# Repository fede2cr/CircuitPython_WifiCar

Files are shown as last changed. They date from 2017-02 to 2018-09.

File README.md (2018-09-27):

# Guía de construcción y uso del WifiCar con CircuitPython

# For english go to [this version](https://github.com/fede2cr/CircuitPython_WifiCar/blob/master/README.en.md)

## Instrucciones
### Realizar conexión física

Se recomienda que el soldado de los stacking headers y terminales sea realizado previo al taller. De esta forma la única herramienta necesaria sería un desatornillador de punta phillips para ensamblaje del chasis.

- Soldar stacking headers en el ESP8266 y el Featherwing para motor
- Soldar terminales de tornillo en Featherwing para motor
- Poner baterías en holder
- Conectar holder de baterías a puerto de batería para motor, del Featherwing para motores

La tarjeta debería verse de esta forma:

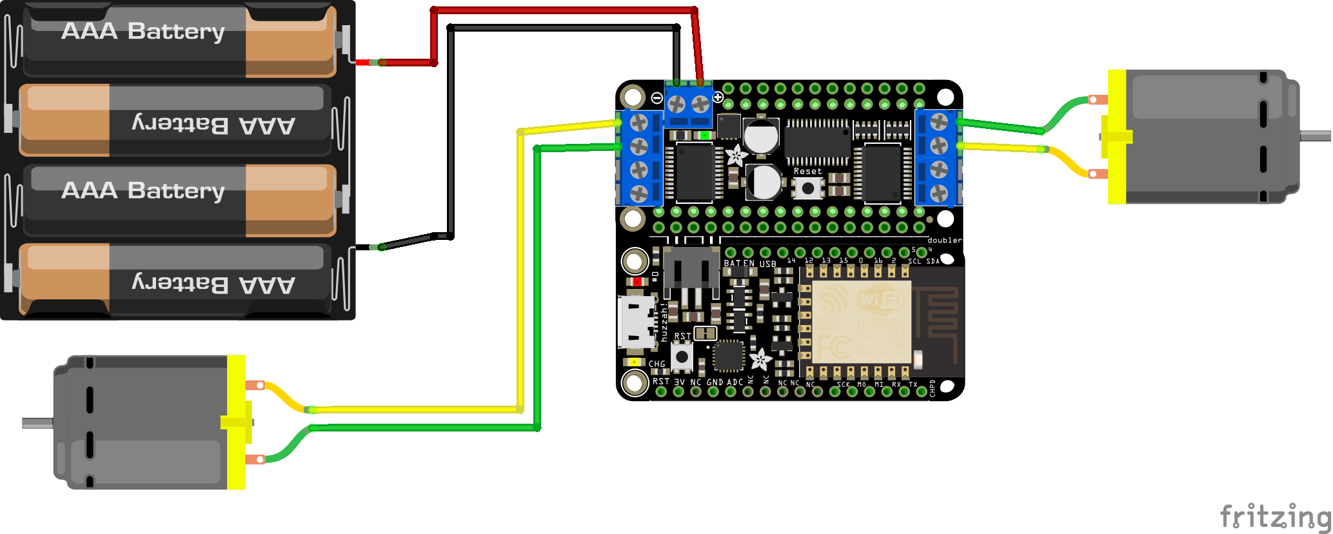
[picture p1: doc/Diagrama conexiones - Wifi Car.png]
Diagrama de Fritzing


### Instalar CircuitPython en ESP8266

Se carga firmware según [instrucciones de Adafruit](https://learn.adafruit.com/micropython-basics-how-to-load-micropython-on-a-board/?view=all#esp8266), pero usando release de CircuitPython

```bash
esptool.py --port /dev/ttyUSB0 erase_flash
esptool.py --port /dev/ttyUSB0 --baud 460800 write_flash --flash_size=detect 0 adafruit-circuitpython-feather_huzzah-es-4.0.0-alpha.1.bin
```
Reiniciar el ESP8266, y comprobar que se puede acceder al REPL de CircuitPython, conectándose al puerto serial
```
screen /dev/ttyUSB0 115200
```
Puede salir de screen digitando ``CTRL+A`` y luego ``:quit``.

### Módulos de CircuitPython

Luego debe descargar los módulos de CircuitPython de Featherwing de motor, de Register Bus Device; los cuales tanto para evitar una [pulga](https://github.com/adafruit/Adafruit_CircuitPython_PCA9685/issues/3) como para simplificar, vamos a utilizar el ["Bundle"](https://github.com/adafruit/Adafruit_CircuitPython_Bundle/releases). Luego utilice la herramienta de ``ampy`` para subir las **carpetas** de los módulos al flash de la ESP8266:

```bash
export AMPY_PORT=/dev/ttyUSB0
unzip adafruit-circuitpython-bundle-2.*.zip
ampy put lib 
ampy ls
```
Ahora puedes probar un pequeño "hola mundo" para comprobar que has subido los módulos de forma correcta, y que has conectado correctamente las baterías y motores. Para esto debes ejecutar de nuevo el comando de `screen` para entrar en el REPL de CircuitPython.
**Nota: Si todo funciona correctamente, el carro se va a mover hacia adelante. Acomódelo de forma que no se caiga de la mesa de trabajo**
```python
from board import *
import bitbangio as io
i2c = io.I2C(SCL, SDA)
from adafruit_pca9685 import motor
motors = motor.DCMotors(i2c)
motors.speed(0, 2000)
motors.speed(3, 2000)
```
*Nota: Es posible que el número del motor haya cambiado, por lo que puedes probar cambiando el motor a mover*
Habiendo comenzado a moverse, el robot solo se va a detener hasta que se agoten las baterías. Para ello digitamos el siguiente comando por cada motor, para iniciar el frenado:

```python
motors.brake(0)
motors.brake(3)
```

### Acceso por Wifi
Esta es una parte que también puede ser preconfigurada en la tarjeta antes de entregar al estudiante, dependiendo de la naturaleza del laboratorio a realizar.
A como viene el firmware de CircuitPython de Adafruit, el ESP8266 se va a comportar como un Access Point wireless, por lo que queremos conectarlo a la red a utilizar durante el curso o taller. También es importante que se configure antes de pasar al sección de WebREPL.

Es importante que la configuración de Wifi no debe ser guardada en `boot.py` dado que es almacenada de forma interna por CircuitPython. Para ello ejecutamos desde el REPL.

```python
import network
wlan = network.WLAN(network.STA_IF)
wlan.active(True)
wlan.connect('nombre-AP-curso','clave-segura')
```
Luego de unos segundos estará conectado a la red, lo que puede comprobar ejecutando:
```python
wlan.ifconfig()
```

### WebREPL
El WebREPL ya casi se encuentra listo para ser usado. Primero debes importar el módulo de `webrepl_setup` el cual se encarga de habilitar WebREPL de forma permanente, así como definir una contraseña de acceso.

*Nota: CircuitPython no tiene límite de conexiones por lo que es fácilmente atacable por fuerza bruta con listas de diccionario. Por ello, fuera de un ambiente académico se recomienda o utilizar una contraseña segura o deshabilitar WebREPL*.

```python
>>> import webrepl_setup
WebREPL daemon auto-start status: disabled

Would you like to (E)nable or (D)isable it running on boot?
(Empty line to quit)
> e
To enable WebREPL, you must set password for it
New password: greencore
Confirm password: greencore
Changes will be activated after reboot
Would you like to reboot now? (y/n) y

```

Luego de este paso, la tarjeta debería reiniciar automáticamente y dejarnos con el WebREPL activado. Por [mientras](https://github.com/adafruit/circuitpython/issues/98) debes reiniciar la tarjeta manualmente presionando el botón de RESET ya sea en la ESP8266 o en el Featherwing de motores.

Para accesar el WebREPL normalmente deberíamos bajar un  [cliente desde esta dirección](https://github.com/micropython/webrepl/archive/master.zip), descomprimir, y abrir con Firefox o Chromium. Defines el IP que tiene actualmente el ESP8266, presionas *Conectar* y digitas la contraseña definida. Ya puedes digitar comandos en la microcontroladora desde el WebREPL, incluidos comandos para los motores y otros. En este proyecto sin embargo se ha incluído funcionalidad Web para que la página de WebREPL sea servida directamente desde la ESP8266.

Así mismo vamos a agregar código a `boot.py` para que pueda servir su propio repositorio de WebREPL para no necesitar un servidor adicional o conexión a Internet. El código de ello se basa en [replserver](https://github.com/ShrimpingIt/cockle/blob/master/replserver/)

Para subir el WebREPL auto-servido, debemos agregar la página web minimizada y comprimida, ejecutando:
```bash
ampy put webrepl-inlined.html.gz
```

### Autoconfiguración

Para evitar que tengamos que digitar las operaciones que definen el motor, vamos a agregar estos comandos iniciales al archivo `boot.py` de forma que cuando inicie la micro, automáticamente va a configurar la tarjeta de motor shield, para que sea más sencillo y podamos digitar comandos de motores de forma directa.

Para ello es buena idea revisar si nuestro archivo `boot.py` posee algún código importante, sin embargo en nuestro caso como hemos comenzado desde cero, es posible omitir este paso. Para revisarlo puede ejecutar:
```bash
ampy get boot.py
```
En nuestro caso, vamos a usar el archivo como base, descomentando las líneas que deshabilitan *debugging*, el cual se encuentra habilitado porque CircuitPython se encuentra en un estado muy activo de desarrollo.
Agregamos las líneas de iniciado de motor y librerías que vimos arriba, y subimos el archivo a nuestra ESP8266.
```bash
ampy put boot.py
```

Después de reiniciar nuestro ESP8266 ya podemos ejecutar comandos de motores:
```python
motors.speed(0, 2000)
motors.speed(3, 2000)
```
Recuerde que el comando actual no ejecuta ningún frenado por lo que luego debe ejecutar:

```python
motors.brake(0)
motors.brake(3)
```

### Clase de Python para manejo de carro

Hasta el momento tenemos un carro que podemos controlar vía Web sobre Wifi. Sin embargo los controles de dicho carro son un poco diferentes a las formas como conducimos algún tipo de carro eléctrico, ya sea de control remoto, un GoCart o un Tesla.

Para ello se crea una pequeña clase de Python donde se pueda controlar de forma sencilla. Se asume que el robot no tiene sensores como giroscopios o rotary encoder, por lo cual algunos movimientos deben ser calibrados y aproximados.

El cargado de esta clas ya se ejecuta automáticamente al inicio del robot por medio de `boot.py`.

Para cargar la clase debe ejecutar en la terminal:
```bash
ampy put Robot.py
ampy ls
```
Ahora puede conectarse al robot usando ya sea `screen` o WebREPL, y dentro ejecutar:

```python
carro.adelante(segundos)
carro.izquierda(segundos)
carro.hola() # Un demo mínimalista
```

También se pueden crear geometrías sencillas definiendo la **cantidad de lados**, el **largo de las líneas en segundos**, y el **tiempo que debería durar girando para hacer el ángulo correcto**. Es importante calibrar el tiempo para el ángulo dado que va a cambiar según la superficie, tracción de las ruedas y carga/tipo de baterías para los motores:
```python
carro.geometria(3, 1, 0.9) # Un triángulo pequeño
carro.geometria(4, 2, 0.7) # Un cuadrado
```

Así mismo, se deben crear demostraciones de comportamiento, las cuales pueden ser cargadas como una clase de ejemplos:
```python
carro.demo(sillywalks) # Como MonthyPython
carro.demo(wifitaxa)   # Camina hacia el access point
```

## Referencias
- [Corriendo código y uso de Ampy](https://learn.adafruit.com/micropython-basics-load-files-and-run-code/?view=all)
- [Featherwing de motores](https://learn.adafruit.com/micropython-hardware-pca9685-dc-motor-and-stepper-driver/?view=all)
- [WebREPL](https://learn.adafruit.com/micropython-basics-esp8266-webrepl/?view=all)
- [TonyD's WebREPL Robot](https://www.youtube.com/watch?v=hOwReBsHq7g)
- [replserver](https://github.com/ShrimpingIt/cockle/blob/master/replserver/)

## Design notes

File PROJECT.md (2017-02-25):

# CircuitPython_WifiCar
Carro controlado por medio de Wifi, basado en la micro ESP8266 con el lenguaje educativo CircuitPython, basado en Micropython

Este documento describe las labores a realizar. Una vez que el proyecto tenga avance, el documento [HOWTO.md](https://github.com/fede2cr/CircuitPython_WifiCar/blob/master/HOWTO.md) reemplazará buena parte de este README.

## Descripción
Greencore Solutions ya tiene un curso de robótica para niños basado en micros Arduino, donde los estudiantes construyen su carro de dos motores el cual es manejado con un control remoto infrarojo, al cual queremos mejorar lo siguiente:

1. El control infrarojo de un estudiante acciona los carros de otros estudiantes por lo que necesitamos cambiar la forma de control remoto.
2. El lenguaje de Arduino se basa en C/C++ por lo que no es la mejor opción para estudiantes completamente novatos. Para ello se recomienda migra a MicroPython o mejor aún a CircuitPython.
3. La micro ofrecida anteriormente tenía un acelerómetro lo que permitía que estudiantes avanzados comenzaran a hacer detección de golpe y otros comportamientos. La micro actual es un poco básica por lo que requiere hardware adicional para permitir que sea interesante para estudiantes avanzados.

## Propuesta
Cambiar a la plataforma de [Feather de Adafruit](https://www.adafruit.com/feather), con los siguientes componentes:

- Adafruit ESP8266 Feather: La plataforma ESP8266 es compatible con Arduino si fuera necesario, tiene conector JST para batería (con capacidad de cargar baterías Lipo), capacidades de red inalámbrica Wifi, así como trabaja con CircuitPython/Micropython.
- Adafruit DC Motor+Stepper Featherwing: Tiene capacidad de hasta cuatro motores lo que permite usar cualquier de los chasis disponibles en [CrCibernetica](http://crcibernetica.com/).

### Cambios menores:
- Cambiar lugar de baterías AAA por posición más accesible. Actualmente hay que desarmar parcialmente el robot para cambio de baterías. Es posible alimentar los motores de 4.5VDC a 13.5VDC por lo que se podría cambiar a baterías 9V u otras.

## Plan de trabajo
- [x] Alistar componentes de hardware: Soldar stacing headers en Feather y Featherwing, remover placa anterior, alistar conectores de batería.
- [x] Instalar última versión de CircuitPython en la ESP8266
- [x] Ensamblar robot con nueva micro y realizar control básico de motores.
- [x] Usar como base WebREPL para crear una librería que permita control del robot por medio de una página web servida por el mismo ESP8266.
- [ ] Crear documentación visual de ensamblaje de robot.
- [ ] Crear diversos laboratorios que el estudiante pueda seguir para sacarle un mejor provecho a su robot ensamblado y completo.
- [ ] Crear traducciones de la documentación
- [ ] Crear clases que permitan crear alias para comandos en otros idiomas (forward=adelante, etc)
- [ ] Probar librería de selector de Wifi, para mejorar la portabilidad del proyecto

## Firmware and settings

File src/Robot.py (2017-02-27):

# RobotControl
# Cualquier posible sensor va a estar apagado por omisión
# Los comandos de movimiento deberían ser similares a los de LogoWriter

# Uso ejemplo:
#   import Robot
#   robot = Robot.Control(motors)
#   robot.adelante(10)
# Autor: Alvaro Figueroa (alvaro@greencore.co.cr)
import time

class Control:
    def __init__(self, motors):
        self._motors = motors
        self._motors.brake(0)
        self._motors.brake(3)

    def adelante(self, secs):
        self._motors.speed(0,2000)
        self._motors.speed(3,2000)
        time.sleep(secs)
        self._motors.brake(0)
        self._motors.brake(3)

    def atras(self, secs):
        self._motors.speed(0,-2000)
        self._motors.speed(3,-2000)
        time.sleep(secs)
        self._motors.brake(0)
        self._motors.brake(3)

    def derecha(self, secs):
        self._motors.speed(0,2000)
        self._motors.speed(3,-2000)
        time.sleep(secs)
        self._motors.brake(0)
        self._motors.brake(3)

    def izquierda(self, secs):
        self._motors.speed(0,-2000)
        self._motors.speed(3,2000)
        time.sleep(secs)
        self._motors.brake(0)
        self._motors.brake(3)

    def hola(self):
        self.adelante(1)
        self.atras(1)
        self.derecha(1)
        self.izquierda(1)

    def geometria(self, lados, largo_secs, angulo_secs):
        for i in range(lados):
            self.adelante(largo_secs)
            self.izquierda(angulo_secs)

    def sillywalk_serpiente(self,secs):
        for i in range(4):
            self._motors.speed(0,4000)
            self._motors.speed(3,2000)
            time.sleep(secs/8)
            self._motors.speed(0,2000)
            self._motors.speed(3,4000)
            time.sleep(secs/8)
        self._motors.brake(0)
        self._motors.brake(3)

    def sillywalk_turn(self,secs):
        for i in range(4):
            self._motors.speed(0,4000)
            self._motors.speed(3,-4000)
            time.sleep(secs/8)
            self._motors.speed(0,-4000)
            self._motors.speed(3,4000)
            time.sleep(secs/8)
        self._motors.brake(0)
        self._motors.brake(3)


    def ayuda(self):
        print("""Modulo de control de robot.
Comandos:
carro.hola()                    Realiza una demostracion de movimientos
carro.adelante(segundos)        Avanza la cantidad de segundos que se indique
carro.atras(segundos)           Retocede la cantidad de segundos que se indique
carro.derecha(segundos)         Gira sobre su eje a la derecha, la cantidad de
                                segundos que se indique
carro.izquierda(segundos)       Gira sobre su eje a la izquierda, la cantidad de
                                segundos que se indique
carro.geometria(lados,
   largo_secs, angulo_secs)     Le indicamos la cantidad de lados, que tan
                                largos en segundos, cuanto tiempo durar girando,
                                y nos crea una figura geometrica

Ejemplos:
carro.hola()
carro.adelante(2)
carro.izquierda(1)
carro.atras(3)
carro.geometria(4, 2, 0.7)
Puede encontrar informacion adicional en
https://github.com/fede2cr/CircuitPython_WifiCar/""")

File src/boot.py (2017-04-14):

# This file is executed on every boot (including wake-boot from deepsleep)
import esp
esp.osdebug(None)
import gc
gc.collect()

import network
wlan = network.WLAN(network.STA_IF)
wlan.active(True)

from board import *
import bitbangio as io
i2c = io.I2C(SCL, SDA)
from adafruit_pca9685 import motor
motors = motor.DCMotors(i2c)
motors.brake(0)
motors.brake(3)

import Robot
carro = Robot.Control(motors)

# replserver boot code
try:
    import usocket as socket
except:
    import socket

import os
import webrepl
webrepl.start(password='greencore')
replpath = "webrepl-inlined.html.gz"

s = socket.socket()
ai = socket.getaddrinfo("0.0.0.0", 80)
addr = ai[0][-1]

s.setsockopt(socket.SOL_SOCKET, socket.SO_REUSEADDR, 1)
s.bind(addr)
s.listen(5)

def accept_handler(sock):
        res = sock.accept()
        print("Handling")
        client_s = res[0]
        string_request = client_s.recv(2048).decode('utf-8')
        print("Request:" + string_request)
        try:
                request_line = string_request.split("\r\n")[0]    # only consider first line
                request_line = request_line.split()     # separate by whitespace
                (request_method, path, request_version) = request_line
                header = ''
                content = ''
                if request_method == "GET" and "favicon" not in path:
                        print("GET "+ path)
                        header += 'HTTP/1.1 200 OK\r\n'
                        header += 'Content-Type: text/html; charset=UTF-8\r\n'
                        header += 'Content-Encoding: gzip\r\n'

                        replsize = os.stat(replpath)[6]
                        header += 'Content-Length: ' + str(replsize) + '\r\n'
                        header += '\r\n'

                        client_s.send(header)
                        print("Sent "+ header)

                        with open(replpath, 'r') as f:
                                chunkCount = 0
                                while True:
                                        chunk = f.read(1024)
                                        if chunk != '':
                                                client_s.write(chunk)
                                                print("Sent chunk " + str(chunkCount) + ":" + str(len(chunk)))
                                                chunkCount = chunkCount + 1
                                        else:
                                                print("Last chunk sent")
                                                break
        except Exception as e:
                print("Exception", e)
        finally:
                client_s.close()

s.setsockopt(socket.SOL_SOCKET, 20, accept_handler)

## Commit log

2017-02-17 Agregando README, y diagrama de Fritzing
    [Diagrama conexiones - Wifi Car.fzz]
2017-02-20 Agregando información a Readme, y agregando archivo HOWTO.md. Se refresca el diagrama para usar las actuales baterías 4xAAA
    [Diagrama conexiones - Wifi Car.fzz]
2017-02-20 Typos de markdown en HOWTO.md
2017-02-20 Completa la guía de HOWTO, falta implementación de nueva clase, se agrega src/boot.py
2017-02-20 Usando una comilla de ejecución para código en MD dentro del HOWTO. Agregando enlace al HOWTO desde el README
2017-02-22 Actualizando a CP 0.9.0, cambiando orden de zips/puts, typo 'ampy push'
2017-02-24 Se agrega clase para manejo sencillo del robot, así como se actualiza la doc para su instalación y ejecución
2017-02-24 Agregando funcion para dibujar geometrias
2017-02-24 WebREPL ahora es una página auto-servida por el ESP8266
2017-02-25 Agregando la tarea de buscar un selector de Wifi, al README
2017-02-27 Agregando dos carro.sillywalks_...(), y carro.ayuda(), y arreglando sillywalks en el howto
    [Robot.py]
2017-02-28 Moviendo README hacia PROJECT, y HOWTO hacia README. Agregando la mitad de la traducción a inglés
2017-03-23 Upgrade a Circuitpython 0.9.1
2017-04-11 New circuitpython release
2017-04-24 Upgrade to circuitpython 0.9.6
2017-05-10 Release de circuitpython 0.9.7
2017-05-19 Circuitpython relase to 0.10.0
2017-06-23 Upgraded to CircuitPython 1.0.0.rc.2
2017-06-30 Upgrade circuitpython a 1.0.0-rc.3
2017-07-07 Upgrade a circuitpython 1.0.0-rc.4
2017-09-16 Upgrade a circuitpython 2.0.0
2017-09-25 Usando bundle de circuitpython para esquivar pulga en release de librería de motor
2017-09-25 EN: Using the circuitpython bundle for easyer use and to workaround a bug in the mpy release of the motor module
2017-11-16 Actualizando a circuitpython 2.1.0
2018-04-23 Upgrade to circuitpython (stable) 2.2.4
2018-05-17 Upgrade and validation with CircuitPython 2.3.1
2018-08-21 Actualizando a CircuitPython 3.0.1
2018-09-27 Actualizando a CP 4 alpha, con soporte de idioma
